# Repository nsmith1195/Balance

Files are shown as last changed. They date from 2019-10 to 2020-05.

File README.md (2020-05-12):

# Balance
<p align="center">
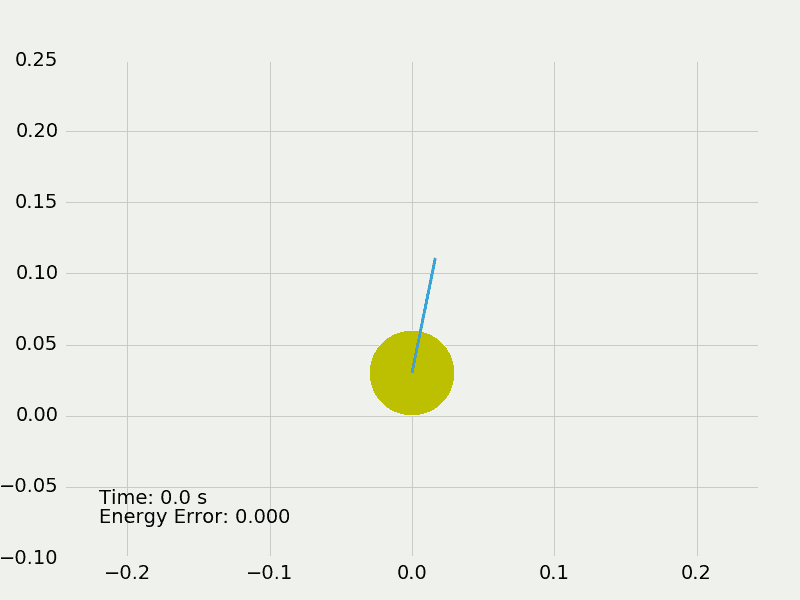
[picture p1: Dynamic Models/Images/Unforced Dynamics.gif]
  
  
</p>

Balancing Robot Repository

Robot acts as an inverted pendulum with the goal of remaining stable while being mobile in at least one direction. Turning may be added as a later feature as wheels are independently actuated. A full report on this project can be found in Final.pdf which includes relevant derivations and explanations for design choices. Below is a short summary of each major section.

## Dynamic Model
The full equations of motion were derived for a Wheeled Inverted Pendulum (WIP) and were used to simulate the system with Scipy. It is assumed that the robot can only move in a straight line which greatly simplifies the calculations. This model was then linearized and used to generate several control laws. 

## Controller Design
To simplify the initial design the linearized model was further reduced to a single input single output transfer function relating the angle of the robot to the torque input. This allows the use of very simple frequency domain design tools such as the root locus, as well as the use of common control architectures like PD and direct feedback.

## Mechanical Design
The body of the robot is mostly composed of secondhand parts from various electronics. Several small parts such as wheel connectors were 3D modeled and printed.

## Electrical Design
The controller for the robot is an Arduino Uno which draws power from the 5 volt regulator on an L298 motor driver. This driver provides power for both motors. To allow for direct control of the torque to each motor, current sensing resistors are placed in series with each motor. To read each voltage a difference amplifier is used to amplify the small voltage drop and allow reading by the Arduinio ADC. Finally, to measure the state of the robot an MPU-6050 inertial measurement unit and quadrature encoders allow direct measurement of the angle and distance travelled. To manage many of these components a breadboard is mounted opposite from the Arduino where each component can easily attach.

## Software Design

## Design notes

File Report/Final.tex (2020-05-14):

\documentclass{article}
\title{Development Of A Wheeled Inverted Pendulum}
\author{Nathan Smith}
\date{April 8th, 2020}

\usepackage{graphicx}
\usepackage{subcaption}
\usepackage{placeins}
\usepackage[margin=1.0in]{geometry}	%Change the page margins to fit long equations
\usepackage{amsmath}

\graphicspath{{"../Report/Images/"}}

%\renewcommand*{\vec}[1]{\mathbf{#1}} %Redefine vector command to make bold instead of overhead arrow

\begin{document}
	\pagenumbering{gobble}
	\maketitle
	
	\newpage
	\tableofcontents

	\newpage
	\pagenumbering{arabic}	
	
	\section{Dynamic Model}
	\subsection{Derivation}
	
	\begin{figure}[h]
		}
		\caption{Overview and Definitions}	
		\label{fig:System Definitions}	
	\end{figure}
	
	As shown in \ref{fig:System Definitions} the configuration of the system is given by x and $\theta$. The variable $\phi$ is the rotation of the wheel relative to the vertical axis and is completely determined by x:
	
	\centerline{$x = r\phi$ and	$\dot{x} = r \dot{\phi}$}
	
	Positive translations are to the right and position rotations are clockwise. Also a positive torque is one which tends to make the WIP accelerate in the positive direction (and cause a negative rotation).

	Since there are two bodies in this system the Euler-Lagrange equation will be used to derive the equations of motion for the WIP:
	\begin{equation}
		\label{eqn:EulerLagrange}	
		\frac{d}{dt}\left(\frac{\partial L}{\partial \dot{q}_i}\right) - \frac{\partial L}{\partial q_i} = F_i
	\end{equation}
	
	where $q = \lbrace x,\theta \rbrace$ are the generalized coordinates defining the configuration of the system and $F = \lbrace \frac{\tau}{r}, -\tau \rbrace$ are the generalized forces acting on each axis. The Lagrangian is also defined as the difference between the kinetic and potential energies of the system: 
	\begin{equation}
		\label{eqn:LagDef}
		L = K - U
	\end{equation}
	
	The Kinetic energy can be expressed as the sum of the translational and rotational kinetic energies of each body:
	$$K = \frac{1}{2} m_1 {\vert \dot{\vec{x}}_1 \vert}^2 + \frac{1}{2}m_2 {\vert \dot{\vec{x}}_2\vert}^2 + \frac{1}{2}J_1 \dot{\phi}^2 + \frac{1}{2}J_2 \dot{\theta}^2$$
	
	\begin{figure}[h]
		\centering
		}
		\caption{Definitions of $\dot{\vec{x}}_1$ and $\dot{\vec{x}}_2$}	
		\label{fig:VectorDefinitions}	
	\end{figure}
	
	To continue ${\vert \dot{\vec{x}}_1 \vert}^2$ and ${\vert \dot{\vec{x}}_2\vert}^2$ must be evaluated. Given the definitions of these vectors in \ref{fig:VectorDefinitions}:
	
	%Define the x1 vector and solve for the square of its magnitude
	$${\vec{x}_1} = x \hat{i}$$
	$$ \dot{\vec{x}}_1 = \dot{x} \hat{i}$$
	$${\vert \dot{\vec{x}}_1 \vert}^2 = \dot{x}^2$$
	
	%Define the x2 vector and solve for square of its magnitude
	$$\vec{x}_2 = (x + Lsin(\theta)\hat{i} + L cos(\theta) \hat{j}$$
	$$\dot{\vec{x}}_2 = (\dot{x} + Lcos(\theta)\dot{\theta})\hat{i} - Lsin(\theta)\dot{\theta}\hat{j}$$
	$$\vert \dot{\vec{x}}_2\vert = \sqrt{(\dot{x} + Lcos(\theta)\dot{\theta})^2 + (-Lsin(\theta) \dot{\theta})^2}$$
	$$\vert \dot{\vec{x}}_2\vert = \sqrt{\dot{x}^2 + 2Lcos(\theta)\dot{x}\dot{\theta} + L^2 cos^2 (\theta)\dot{\theta}^2 + L^2 sin^2(\theta) \dot{\theta}^2}$$
	$${\vert \dot{\vec{x}}_2\vert}^2 = \dot{x}^2 + 2Lcos(\theta)\dot{x}\dot{\theta} + L^2 \dot{\theta}^2$$
	
	Substituting back into the appropriate terms in the Kinetic energy along with the definition of $\phi$:
	$$K = \frac{1}{2}m_1 \dot{x}^2 + \frac{1}{2}m_2 (\dot{x}^2 + 2Lcos(\theta)\dot{x}\dot{\theta} + L^2 \dot{\theta}^2) + \frac{1}{2}J_1 \frac{\dot{x}^2}{r^2} + \frac{1}{2}J_2 \dot{\theta}^2$$
	$$K = \frac{1}{2}(m_1 + m_2 + \frac{J_1}{r^2})\dot{x}^2 + m_2 Lcos(\theta)\dot{x}\dot{\theta} + \frac{1}{2}(m_2 L^2 + J_2)\dot{\theta}^2$$

	This equation is split into three terms, linear acceleration, angular acceleration, and an interaction term between linear and angular velocity. Therefore it seems reasonable to define an effective mass and moment of inertia as $M = m_1 + m_2 + \frac{J_1}{r^2}$ and $I = m_2 L^2 + J_2$.
	
	Substituting these into the Kinetic energy gives:
	\begin{equation}
		\label{eqn:Kinetic}
		K = \frac{1}{2}M\dot{x}^2 + m_2 Lcos(\theta)\dot{x}\dot{\theta} + \frac{1}{2}I\dot{\theta}^2
	\end{equation}
	
	Potential energy can be found as:
	\begin{equation}
		\label{eqn:Potential}
		U = m_2 gLcos(\theta)
	\end{equation}		
	
	Substituting \ref{eqn:Kinetic} and \ref{eqn:Potential} into \ref{eqn:LagDef} gives the full Lagrangian for the system:
	
	\begin{equation}
		\label{eqn:Lagrangian}
		L = \frac{1}{2}M\dot{x}^2 + m_2 Lcos(\theta)\dot{x}\dot{\theta} + \frac{1}{2}I\dot{\theta}^2 - m_2 gLcos(\theta)
	\end{equation}
	
	The Lagrangian must now be substituted into \ref{eqn:EulerLagrange} for each generalized coordinate. Starting with x:
	
	$$\frac{\partial L}{\partial x} = 0$$
	
	$$\frac{\partial L}{\partial \dot{x}} = M\dot{x} + m_2 Lcos(\theta)\dot{\theta}$$
	$$\frac{d}{dt}\left(\frac{\partial L}{\partial \dot{x}}\right) = M\ddot{x} + m_2 Lcos(\theta)\ddot{\theta} - m_2 Lsin(\theta)\dot{\theta}^2$$
	
	\begin{equation}
		\label{eqn:EOM1}
		M\ddot{x} + m_2 Lcos(\theta)\ddot{\theta} - m_2 Lsin(\theta)\dot{\theta}^2 = \frac{\tau}{r}
	\end{equation}		
	
	Equation \ref{eqn:EOM1} is the first equation of motion for the system. Repeating this for $\theta$ will give the second:
	
	$$\frac{\partial L}{\partial \theta} = -m_2 Lsin(\theta) \dot{x}\dot{\theta} + m_2 gLsin(\theta)$$
	
	$$\frac{\partial L}{\partial \dot{\theta}} = m_2 Lcos(\theta)\dot{x} + I\dot{\theta}$$
	$$\frac{d}{dt} \left( \frac{\partial L}{\partial \dot{\theta}} \right) = m_2 Lcos(\theta)\ddot{x} - m_2 Lsin(\theta)\dot{x}\dot{\theta} + I\ddot{\theta}$$
	
	\begin{equation}
		\label{eqn:EOM2}
		m_2 Lcos(\theta)\ddot{x} - m_2 Lsin(\theta)\dot{x}\dot{\theta} + I\ddot{\theta} + m_2 Lsin(\theta) \dot{x}\dot{\theta} - m_2 gLsin(\theta) = -\tau
	\end{equation}
	
	Equations \ref{eqn:EOM1} and \ref{eqn:EOM2} both depend on $\ddot{x}$ and $\ddot{\theta}$ and must be solved in terms of these simultaneously. Doing this yields:
	
	\begin{equation}
		\label{eqn:linAcc}
		\ddot{x} = - \frac{m_2 LIsin(\theta)}{m_2^2 L^2 cos(\theta) - MI}\dot{\theta}^2 + \frac{m_2^2 L^2 g}{m_2^2 L^2 cos(\theta) - MI}cos(\theta)sin(\theta) - \left[ \frac{I + rm_2 Lcos(\theta)}{r(m_2^2 L^2 cos(\theta) - MI)} \right] \tau
	\end{equation}
	
	\begin{equation}
		\label{eqn:angAcc}
		\ddot{\theta} = \frac{m_2^2 L^2 sin(\theta)}{m_2^2 L^2 cos(\theta) - MI}\dot{\theta}^2 - \frac{Mm_2 gLsin(\theta)}{m_2^2 L^2 cos(\theta) - MI} + \left[ \frac{rM + m_2 L}{r(m_2^2 L^2 cos(\theta) - MI)} \right] \tau
	\end{equation}
	
	These two non-linear equations describe the motion of the system in the configuration space. To make simulation easier these are converted into the state space by adding the velocities associated with each coordinate:
	
	\begin{equation}
		\label{eqn:nonLinSS}
		\begin{bmatrix}
			\dot{x} 		\\
			\ddot{x}		\\
			\dot{\theta}	\\
			\ddot{\theta}
		\end{bmatrix}
		=		
		\begin{bmatrix}
			\dot{x}			\\
			-\frac{m_2 LIsin(\theta)}{m_2^2 L^2 cos(\theta) - MI}\dot{\theta}^2 + \frac{m_2^2 L^2 g}{m_2^2 L^2 cos(\theta) - MI}cos(\theta)sin(\theta)			\\
			\dot{\theta}	\\
			\frac{m_2^2 L^2 sin(\theta)}{m_2^2 L^2 cos(\theta) - MI}\dot{\theta}^2 - \frac{Mm_2 gLsin(\theta)}{m_2^2 L^2 cos(\theta) - MI}
		\end{bmatrix}
		+
		\begin{bmatrix}
			0																	\\
			-\frac{I + rm_2 Lcos(\theta)}{r(m_2^2 L^2 cos(\theta) - MI)}		\\
			0																	\\
			\frac{rM + m_2 L}{r(m_2^2 L^2 cos(\theta) - MI)}
		\end{bmatrix}
		\tau
	\end{equation}
	
	\subsection{Linearization}
	Equation \ref{eqn:nonLinSS} can be easily simulated with tools such as Scipy's ODEint function to create a reasonable representation of the system. It is not, however, easy to develop control laws for a non-linear system and so it is necessary to linearize it. This will be done about the upwards stationary point $\vec{x}^* = [x, 0, 0, 0]^T$. There is an x in this state since there is a symmetry in x. Currently the system is of the form:
	
	\centerline{$\dot{\vec{x}} = \vec{f}(\vec{x},u)$, where in this case $u = \tau$}
	Linearizing would put the system into the form:
	$$\dot{\vec{x}} = A\vec{x} + Bu$$
	
	To generate A and B the following formula must be applied:
	$A = \left[ \frac{\partial \vec{f}(\vec{x},u)}{\partial \vec{x}} \right]_{x^*,u^*}$ and $B = \left[ \frac{\partial \vec{f}(\vec{x},u)}{\partial u} \right]_{x^*,u^*}$
	
	Doing so yields:
	
	\begin{equation}
		\label{eqn:linSS}
		A = \begin{bmatrix}
			0 & 1 & 0 & 0	\\
			0 & 0 & \frac{m_2^2 L^2 g}{m_2^2 L^2 - MI} & 0 \\
			0 & 0 & 0 & 1	\\
			0 & 0 & -\frac{Mm_2 gL}{m_2^2 L^2 - MI} & 0
		\end{bmatrix}
		\quad and	\quad B = \begin{bmatrix}
			0	\\
			-\frac{I + rm_2 L}{r(m_2^2 L^2 - MI)}	\\
			0	\\
			\frac{rM + m_2 L}{r(m_2^2 L^2 - MI)}
		\end{bmatrix}
	\end{equation}
	
	The output equation will initially return only $\theta$ and so will be:
	
	$y = \vec{C} \vec{x} + Du$, where $\vec{C} = [0, 0, 1, 0] and D = 0$ 
	
	\subsection{Transfer Function}
	Due to some quirks in the Python-Controls library with regards to analyzing state space models, the state space representation derived will be converted into a transfer function to make analysis easier to interpret. Doing so uses:
	
	\begin{equation}
		\label{eqn:SS2TF}
		\frac{\theta (s)}{\tau (s)} = \vec{C}(sI - A)^{-1}\vec{B} + D
	\end{equation}
	
	Applying this to the current system gives:
	
	\begin{equation}
		\label{eqn:SISOTF}
		\frac{\theta (s)}{\tau (s)} = \frac{a}{s^2 - b}
	\end{equation}
	
	\centerline{where $a = \frac{rM + m_2 L}{r(m_2^2 L^2 - MI)}$ and $b = -\frac{Mm_2 gL}{m_2^2 L^2 - MI}$}

	\section{Controller Design}
	\subsection{Plant analysis}
	
	\begin{figure}[h]
		\centerline{}}
		\caption{Pole Zero map of the transfer function. The two poles are real and symmetric, one always in the right half plane.}
		\label{fig:PlantPZMap}	
	\end{figure}	
	
	Figure \ref{fig:PlantPZMap} shows the pole zero map of equation \ref{eqn:SISOTF}, it can be seen that one of the poles is in the right half plane and so the system is unstable. 
	
	\subsection{Direct Feedback Design with Root Locus}
	
	\begin{figure}[h]
		\centerline{}
		\caption{Root locus plot of the plant. Larger gains only yield marginal stability.}
		\label{fig:DirectFeedRL}
	\end{figure}
	
	As a first attempt to stabilize the WIP a simple gain controller was implemented in the simulation. As shown in figure \ref{fig:DirectFeedRL} the system is unstable for low gains and only achieves marginal stability with larger gains. This is not acceptable as a solution but does make for an interesting animation which can be seen in the readme for this project.
		
	\subsection{PD Design}
	While continuous time PD controllers are not realizeable, the fact that my simulation provides access to the entire state of the system I am able to sidestep this limitation though when it is implemented on hardware the controller will need to be discretized. The usual form of a PD controller is:
	
	\begin{equation}
		\label{eqn:PDController}
		C(s) = k_d s + k_p
	\end{equation}
	
	This equation has two parameters to vary and so makes traditional design techniques such as root locus design difficult. By factoring out $k_d$ this becomes slightly easier since the pole can be placed by hand at the point $-\frac{k_p}{k_d}$ and $k_d$ can be used as the root locus gain. Doing this gives the modified PD transfer function:
	
	\begin{equation}
		\label{eqn:PDModified}
		C(s) = k_d (s + \frac{k_p}{k_d})
	\end{equation}
	
	The PD controller effectively adds a zero to the function and in this form the ratio $\frac{k_p}{k_d}$ decides that zero's location. Since both system poles and the zero are on the real axis, the zero can either be between the open loop poles $\frac{k_p}{k_d} < b$ or to the left of them $\frac{k_p}{k_d} > b$. To get reasonably quick dynamics the latter case should be selected. 
	
	\begin{figure}[h]
		\centerline{}
		\caption{Root Locus plot of the plant with a PD controller. K value in image is $k_d$ and the location of the zero is $-\frac{k_p}{k_d}$}
		\label{fig:PDRootLocus}
	\end{figure}
	
	The right plot of figure \ref{fig:PDRootLocus} shows the more desirable case. As can be seen in that plot from the annotated gains, even a gain as small as 0.12 will move the dominant pole very close to the zero. The non-dominant pole is far in the negative direction and was excluded from the figure in the interest of maintaining a reasonable scale and readability.

\section{Mechanical Design}

	\begin{figure}[h]
		\centerline{}
		\caption{Expected setup of robot body. Some areas such as the method of attaching the wheels are still undetermined.}		
		\label{fig:RobotBodyGraphic}
	\end{figure}

	\subsection{Part Sourcing}
	Due to the very limited budget for this project most parts were scavenged from old printers and toys. Most structural parts came from a toy erectors set which allowed for some degree of uniformity in the design due to those components having regularly spaced holes. The motor mounts were made by cutting the entire motor assembly along with the encoders out of an old printer and mounting them in the best possible way to the sides of the body. This approach led to many issues of alignment with regards to the Inertial Measurement Unit (IMU) which required extra effort to calibrate. 	

	\subsection{Custom Parts}
	Since the gears attached to the wheels were not designed to mount the wheels I had on hand, I had to design a custom adaptor to allow the wheels to mount. 
	
	\subsection{Mass Properties}
	Due to the largely unplanned nature of the mechanical design the mass properties of the robot must be measured after each section is assembled. The names for each section of the robot will follow the same convention as the derivation of the equations of motion, namely body 1 references the wheels and body 2 references the main body of the robot. The masses of each are easy to obtain using a standard scale, however the moments of inertia of each are more difficult to establish.

	\begin{figure}[h]
		\centerline{}
		\caption{Experimental setup and diagram of forces acting on body 1. Polar coordinates are initially used to define the location of the body where $\theta$ is the angle of the ramp and x is the distance of the body from the bottom.}
		\label{fig:Body1MassProps}
	\end{figure}		
	
	The moment of inertia of body 1 will be found by rolling it down a long inclined plane and timing it.	 A description of this setup is shown in figure \ref{fig:Body1MassProps}. Polar coordinates were used to define the location of the body with x being the radial distance from the origin. Due to this the velocity found is negative but this decision doesn't change the results. The variable $\phi$ defines the angular position of the body and is related to x through the equation: 
	
											%Definition of phi
	\begin{equation}
		\label{eqn:Body1PropsPhiDefinition}
		L - x = r\phi
	\end{equation}
	
	$$-\dot{x} = r \dot{\phi}$$
	
	\begin{equation}
		-\ddot{x} = r \ddot{\phi}
		\label{eqn:Body1PropsPhiddot}
	\end{equation}
	
	Using the coordinate system in figure \ref{fig:Body1MassProps} force and torque balances can be calculated:
	
	%Force balance in x
	$$\Sigma F_x = ma_x = \mu N - mgsin(\theta)$$
	
	Solving for the coefficient of static friction $\mu$:	
	\begin{equation}
		\mu = \frac{a_x + gsin(\theta)}{gcos(\theta)}
		\label{eqn:Body1PropsMu1}
	\end{equation}
	
	%Torque balance about CG
	The torque balance is done about the body's center of mass:
	$$\Sigma M_{CG} = J\ddot{\phi} = r \mu mgcos(\theta)$$
	
	Again solving for $\mu$:
	\begin{equation}
		\mu = \frac{J\ddot{\phi}}{rmgcos(\theta)}
		\label{eqn:Body1PropsMu2}
	\end{equation}
	
	Equating \ref{eqn:Body1PropsMu1} and \ref{eqn:Body1PropsMu2}:
	$$\frac{a_x + gsin(\theta)}{gcos(\theta)} = \frac{J\ddot{\phi}}{rmgcos(\theta)}$$
	
	Simplifying:
	$$a_x + gsin(\theta) = \frac{J\ddot{\phi}}{mr}$$
	
	Substituting equation \ref{eqn:Body1PropsPhiddot} for $\ddot{\phi}$:
	$$a_x + gsin(\theta) = -\frac{Ja_x}{mr^2}$$
	
	$$\left[ 1 + \frac{J}{mr^2} \right] a_x = -gsin(\theta)$$
	$$a_x = -gsin(\theta)\frac{mr^2}{J + mr^2}$$
	
	Integrating both sides with respect to time:
	$$\int_{v_0}^{v} dv = -gsin(\theta)\frac{mr^2}{J + mr^2} \int_{0}^{t} dt$$
	
	The initial velocity is assumed to be zero:
	$$v = -gsin(\theta)\frac{mr^2}{J + mr^2}t$$
	
	Integrating again:
	$$\int_{L}^{0} dx = -gsin(\theta)\frac{mr^2}{J + mr^2} \int_{0}^{T_f} t dt$$
	
	$$-L = -gsin(\theta)\frac{mr^2}{J + mr^2}\frac{T_f^2}{2}$$
	
	Finally rearranging:
	$$J_{eff} = J + mr^2 = \frac{gmr^2sin(\theta)}{L} \frac{T_f^2}{2}$$
	
	This is the moment of inertia about the contact point with the ground and is the effective moment of inertia of the rolling body.
	
	\begin{figure}[h]
		\centerline{}
		\caption{Comparison between the actual geometry of body 2 and the idealized physical pendulum.}
		\label{fig:Body2MassProps}
	\end{figure}
	The moment of inertia of body 2 can be found relatively simply by noting that it effectively is a physical pendulum. By allowing body 2 to hang by its pivot point with the wheels removed and allowing it to swing freely the natural frequency of oscillation can be measured. This quantity can be used to calculate the moment of inertia for the body about the pivot point. This measured value is about the pivot point of the wheels and can also be expressed about the center of mass of the body. Starting with a torque balance of the pendulum:
	\begin{equation}
		\label{eqn:PhysicalPendTorqueBalance}
		\Sigma M_0 = J_{eff} \alpha = -mgLsin(\theta)
	\end{equation}
	
	To eliminate the non-linearity in $\theta$ only small angles are permitted. This allows the approximation $\theta \approx sin(\theta)$ to be used:
	
	$$\alpha = \frac{d^2 \theta}{dt^2} = -\frac{mgL}{J_{eff}}\theta$$
	
	\begin{equation}
		\label{eqn:PhysicalPendLinearODE}
		\frac{d^2 \theta}{dt^2} + \frac{mgL}{J_{eff}} = 0
	\end{equation}
	
	Using standard methods for solving ODE's, if the solution is assumed to be of the form $\theta = e^{rt}$ then the characteristic equation for this system is:
	$$r^2 + \frac{mgL}{J_{eff}} = 0$$
	$$r^2 = -\frac{mgL}{J_{eff}}$$
	$$r = \pm \sqrt[•]{-\frac{mgL}{J_{eff}}}$$
	$$r = \pm i \; \sqrt[•]{\frac{mgL}{J_{eff}}}$$  % \; is a small space to keep sqrt from overlapping i
	
	Plugging these roots into the assumed solution yields:
	$$\theta = c_1 e^{i \; \sqrt[•]{\frac{mgL}{J_{eff}}}t} + c_2 e^{-i \; \sqrt[•]{\frac{mgL}{J_{eff}}}t}$$
	
	Applying Euler's formula:
	$$\theta = c_1 cos(\; \sqrt[•]{\frac{mgL}{J_{eff}}}t) + i c_2 sin(\; \sqrt[•]{\frac{mgL}{J_{eff}}}t)$$
	
	Taking the real part and applying initial conditions:
	\begin{equation}
		\label{fig:PhysicalPendRealSolution}
		\theta = \theta_0 cos(\; \sqrt[•]{\frac{mgL}{J_{eff}}}t)
	\end{equation}

	%equate to w0 and solve for J_eff
	
	Noting that the argument $\sqrt[•]{\frac{mgL}{J_{eff}}}$ is the natural frequency, $\omega_0$, in terms of angular frequency. This can be expressed in terms of frequency:
	$$\omega_0 = 2\pi f_0$$
	
	$$f_0 = \frac{1}{2\pi} \; \sqrt[•]{\frac{mgL}{J_{eff}}}$$
	
	The frequency can be measured by allowing the body to swing and counting the number of cycles which occur over a set time period. This can now be solved for the effective moment of inertia:
	
	$$2\pi f_0 = \sqrt[•]{\frac{mgL}{J_{eff}}}$$
	
	$$4\pi^2 f_0^2 = \frac{mgL}{J_{eff}}$$
	
	\begin{equation}
		\label{eqn:Body2EffectiveMomentOfInertia}
		J_{eff} = \frac{mgL}{4\pi^2 f_0^2}
	\end{equation}
	
	This effective moment of inertia can be used directly in the dynamic model of the system as it is about the axis of rotation. If the moment of inertia about the center of mass is necessary the parallel axis theorem could be applied to yield:
	$$J_{CG} = \frac{mgL}{4\pi^2 f_0^2} - mL^2$$ 

\section{Electrical Design}
	\subsection{Component Selection}
	To control the robot an Arduino microcontroller was used as it was available at the start of the project. While the Arduino isn't the fastest controller available it should be more than fast enough for this project.
	Both motors will be driven by a single L298-n motor driver circuit. This chip also has a 5 volt regulated output and will be used to provide power to the Arduino and IMU. 
	In order to measure the orientation of the robot an MPU-6050 Inertial Measurement Unit was used.

	\subsection{Motor Parameter Evaluation}
	\begin{figure}[h]
		\centerline{}
		\caption{Overview of setup. $\omega_s$ can be measured directly and related to $\omega_m$ through geometry. The back emf, $e_a$, can be measured directly as well.}
		\label{fig:DirectFeedRL}
	\end{figure}
	
	For a permanent magnet DC motor the following relationships hold\cite{Ogata}:
	$$\tau = KI$$
	$$$$

\section{Software Design}
	\subsection{Component Testing Software}
	
	\subsection{Controller Software}
	
\begin{thebibliography}{9}	%Number 9 doesn't mean anything. The number of digits determines how many refs can be made in bibliography. i.e. 1,6, or 8 would allow up to 9 refs while 13 would allow 99, etc.

	\bibitem{Ogata}
		Katsuhiko Ogata,
		\textit{System Dynamics},
		4th edition,
		2004.

\end{thebibliography}

\end{document}

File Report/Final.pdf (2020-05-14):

# Development Of A Wheeled Inverted Pendulum

Nathan Smith

April 8th, 2020

## Contents

1 Dynamic Model | 1
2 Controller Design | 4
3 Mechanical Design | 5
4 Electrical Design | 9
5 Software Design | 10

## 1 Dynamic Model

### 1.1 Derivation

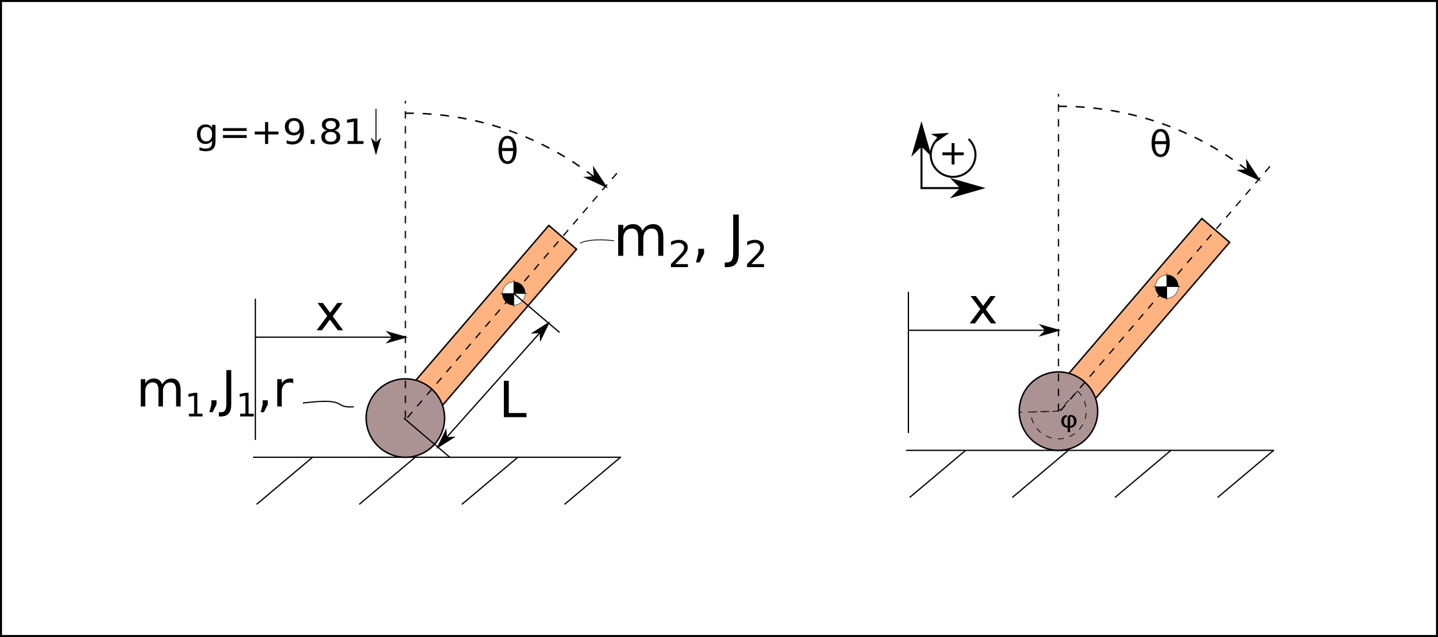
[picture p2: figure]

Figure 1: Overview and Definitions

As shown in 1 the configuration of the system is given by x and θ. The variable φ is the rotation of the wheel relative to the vertical axis and is completely determined by x:
x = rφ and ẋ = rφ˙
Positive translations are to the right and position rotations are clockwise. Also a positive torque is one which tends to make the WIP accelerate in the positive direction (and cause a negative rotation).
Since there are two bodies in this system the Euler-Lagrange equation will be used to derive the equations of motion for the WIP:
d

dt
∂L
∂q˙i
−

∂L
∂qi
= Fi | (1)

where q = {x, θ} are the generalized coordinates defining the configuration of the system and F = {

τ
r
| , −τ}
are the generalized forces acting on each axis. The Lagrangian is also defined as the difference between the kinetic and potential energies of the system:
L = K − U | (2)

The Kinetic energy can be expressed as the sum of the translational and rotational kinetic energies of each body:

K =

1
2

m1|

˙~x1|

2
+

1
2

m2|

˙~x2|

2
+

1
2

J1φ˙² +

1
2

J2

˙θ
2

To continue |

˙~x1|

2
and |

˙~x2|

2
must be evaluated. Given the definitions of these vectors in 2:

~x1 = xî

˙~x1 = ẋî

˙~x1|

2
= ẋ

2

~x2 = (x + Lsin(θ)î + Lcos(θ)ĵ

˙~x2 = ( ẋ + Lcos(θ)
˙θ)î − Lsin(θ)

˙θĵ

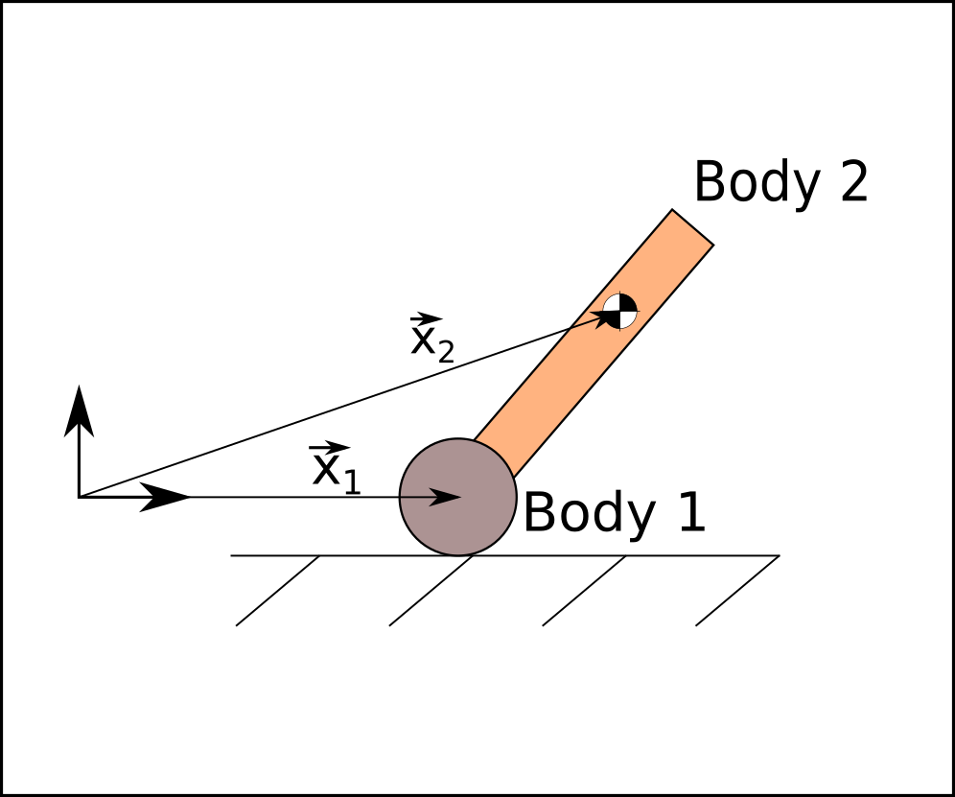
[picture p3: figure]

Figure 2: Definitions of ˙~x1 and ˙~x2

˙~x2| =

q
( ẋ + Lcos(θ)

˙θ)
2 + (−Lsin(θ)

˙θ)
2

˙~x2| =

q
x˙

2 + 2Lcos(θ) ẋ ˙θ + L²cos²(θ)

˙θ
2 + L²sin²(θ)

˙θ
2

˙~x2|

2
= ẋ

2 + 2Lcos(θ) ẋ ˙θ + L

2 ˙θ
2

Substituting back into the appropriate terms in the Kinetic energy along with the definition of φ:

K =

1
2

m1x˙

2 +

1
2

m2( ẋ

2 + 2Lcos(θ) ẋ ˙θ + L

2 ˙θ
2

) + 1
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
(m1 + m2 +

J1
r

2

) ẋ

2 + m2Lcos(θ) ẋ ˙θ +

1
2

(m2L

2 + J2)

˙θ
2

This equation is split into three terms, linear acceleration, angular acceleration, and an interaction term between linear and angular velocity. Therefore it seems reasonable to define an effective mass and moment of inertia as M = m1 + m2 +

J1
r

2 and I = m2L

2 + J2.
Substituting these into the Kinetic energy gives:

K =

1
2

Mx˙

2 + m2Lcos(θ) ẋ ˙θ +

1
2

I

˙θ
2
(3)

Potential energy can be found as:
U = m2gLcos(θ) | (4)

Substituting 3 and 4 into 2 gives the full Lagrangian for the system:

L =

1
2

Mx˙

2 + m2Lcos(θ) ẋ ˙θ +

1
2

I

˙θ
2 − m2gLcos(θ) | (5)

The Lagrangian must now be substituted into 1 for each generalized coordinate. Starting with x:

∂L
∂x = 0

∂L
∂x˙

= Mx˙ + m2Lcos(θ)

˙θ

d

dt
∂L
∂x˙
= Mx¨ + m2Lcos(θ)

¨θ − m2Lsin(θ)
˙θ
2

Mx¨ + m2Lcos(θ)

¨θ − m2Lsin(θ)

˙θ
2 =

τ
r

(6)

Equation 6 is the first equation of motion for the system. Repeating this for θ will give the second:

∂L
∂θ = −m2Lsin(θ) ẋ ˙θ + m2gLsin(θ)

∂L
∂ ˙θ

= m2Lcos(θ) ẋ + I

˙θ

d

dt
∂L
∂ ˙θ
= m2Lcos(θ)ẍ − m2Lsin(θ) ẋ ˙θ + I

¨θ

m2Lcos(θ)ẍ − m2Lsin(θ) ẋ ˙θ + I

¨θ + m2Lsin(θ) ẋ ˙θ − m2gLsin(θ) = −τ | (7)

Equations 6 and 7 both depend on ẍ and ¨θ and must be solved in terms of these simultaneously. Doing this yields:

x¨ = −

m2LIsin(θ)
m²
2L²cos(θ) − MI

˙θ
2 +

m²
2L

2
g
m²
2L²cos(θ) − MI

cos(θ)sin(θ) −

I + rm2Lcos(θ)
r(m²
2L²cos(θ) − MI)
τ | (8)

¨θ =

m²
2L

2
sin(θ)
m²
2L²cos(θ) − MI

˙θ
2 −

Mm2gLsin(θ)
m²
2L²cos(θ) − MI

+

rM + m2L
r(m²
2L²cos(θ) − MI)
τ | (9)

These two non-linear equations describe the motion of the system in the configuration space. To make simulation easier these are converted into the state space by adding the velocities associated with each coordinate:

x˙
x¨
˙θ
¨θ

=

x˙
−

m2LIsin(θ)
m²
2L²cos(θ)−M I

˙θ
2 +

m²
2L

2
g
m²

2L²cos(θ)−M I cos(θ)sin(θ) ˙θ

m²
2L

2
sin(θ)
m²
2L²cos(θ)−M I

˙θ
2 −

Mm2gLsin(θ)
m²
2L²cos(θ)−M I

+

0
−

I+rm2Lcos(θ)
r(m²
2L²cos(θ)−M I)
0
rM+m2L
r(m²
2L²cos(θ)−M I)

τ | (10)

### 1.2 Linearization

Equation 10 can be easily simulated with tools such as Scipy’s ODEint function to create a reasonable representation of the system. It is not, however, easy to develop control laws for a non-linear system and so it is necessary to linearize it. This will be done about the upwards stationary point ~x∗ = [x, 0, 0, 0]T
. There
is an x in this state since there is a symmetry in x. Currently the system is of the form:
˙~x = ~f(~x, u), where in this case u = τ Linearizing would put the system into the form:

˙~x = A~x + Bu

To generate A and B the following formula must be applied: A =

h

∂f~(~x,u)
∂~x i

x∗,u∗

and B =

h

∂f~(~x,u)
∂u i

x∗,u∗
Doing so yields:

A =

0 1 | 0 | 0
0 0 | m² 2L

2
g
m²
| 2L²−M I | 0
0 0 | 0 | 1
0 0 − | Mm2gL
m²
| 2L²−M I | 0

and B =

0
−

I+rm2L
r(m²
2L²−M I)
0
rM+m2L
r(m²
2L²−M I)

(11)

The output equation will initially return only θ and so will be: y = C~x~ + Du, where C~ = [0, 0, 1, 0]andD = 0

### 1.3 Transfer Function

Due to some quirks in the Python-Controls library with regards to analyzing state space models, the state space representation derived will be converted into a transfer function to make analysis easier to interpret. Doing so uses:

θ(s)
τ (s)

= C~ (sI − A)

−1B~ + D | (12)

Applying this to the current system gives:

θ(s)
τ (s)

=

a
s

2 − b

(13)

where a =

rM+m2L
r(m²
2L²−M I)

and b = −

Mm2gL
m²
2L²−M I

## 2 Controller Design

### 2.1 Plant analysis

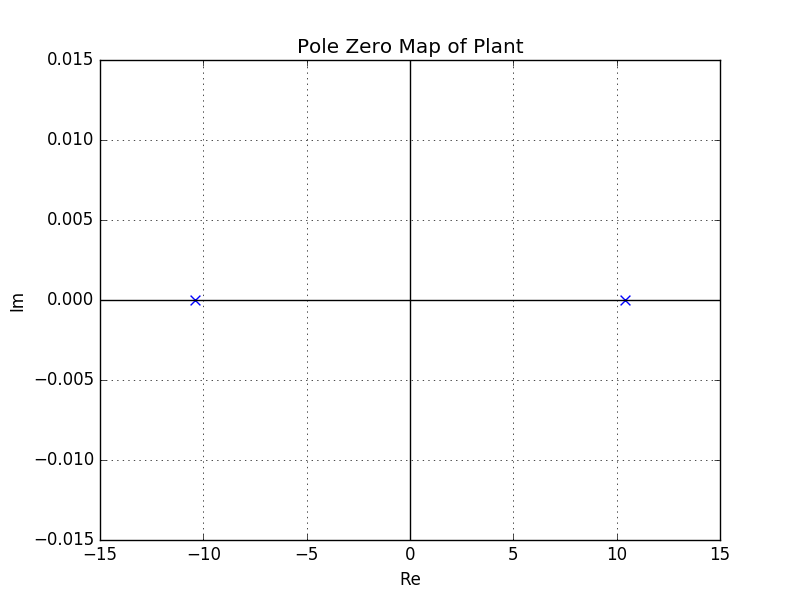
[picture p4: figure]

Figure 3: Pole Zero map of the transfer function. The two poles are real and symmetric, one always in the right half plane.

Figure 3 shows the pole zero map of equation 13, it can be seen that one of the poles is in the right half plane and so the system is unstable.

### 2.2 Direct Feedback Design with Root Locus

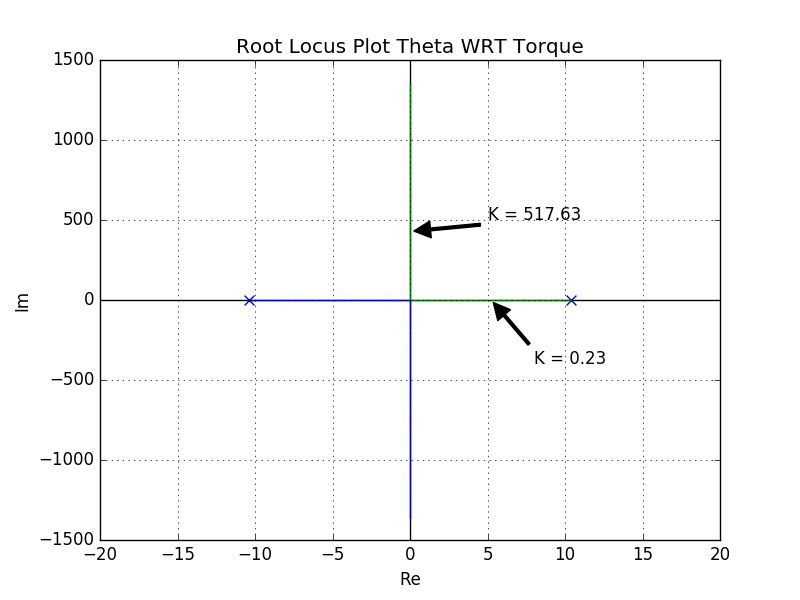
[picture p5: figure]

Figure 4: Root locus plot of the plant. Larger gains only yield marginal stability.

As a first attempt to stabilize the WIP a simple gain controller was implemented in the simulation. As shown in figure 9 the system is unstable for low gains and only achieves marginal stability with larger gains. This is not acceptable as a solution but does make for an interesting animation which can be seen in the readme for this project.

### 2.3 PD Design

While continuous time PD controllers are not realizeable, the fact that my simulation provides access to the entire state of the system I am able to sidestep this limitation though when it is implemented on hardware the controller will need to be discretized. The usual form of a PD controller is:

C(s) = kds + kp | (14)

This equation has two parameters to vary and so makes traditional design techniques such as root locus design difficult. By factoring out kd this becomes slightly easier since the pole can be placed by hand at the point −

kp
kd

and kd can be used as the root locus gain. Doing this gives the modified PD transfer function:

C(s) = kd(s +

kp
kd
) | (15)

The PD controller effectively adds a zero to the function and in this form the ratio kp
kd
| decides that zero’s
location. Since both system poles and the zero are on the real axis, the zero can either be between the open loop poles kp
kd

< b or to the left of them kp
kd

> b. To get reasonably quick dynamics the latter case should be selected.

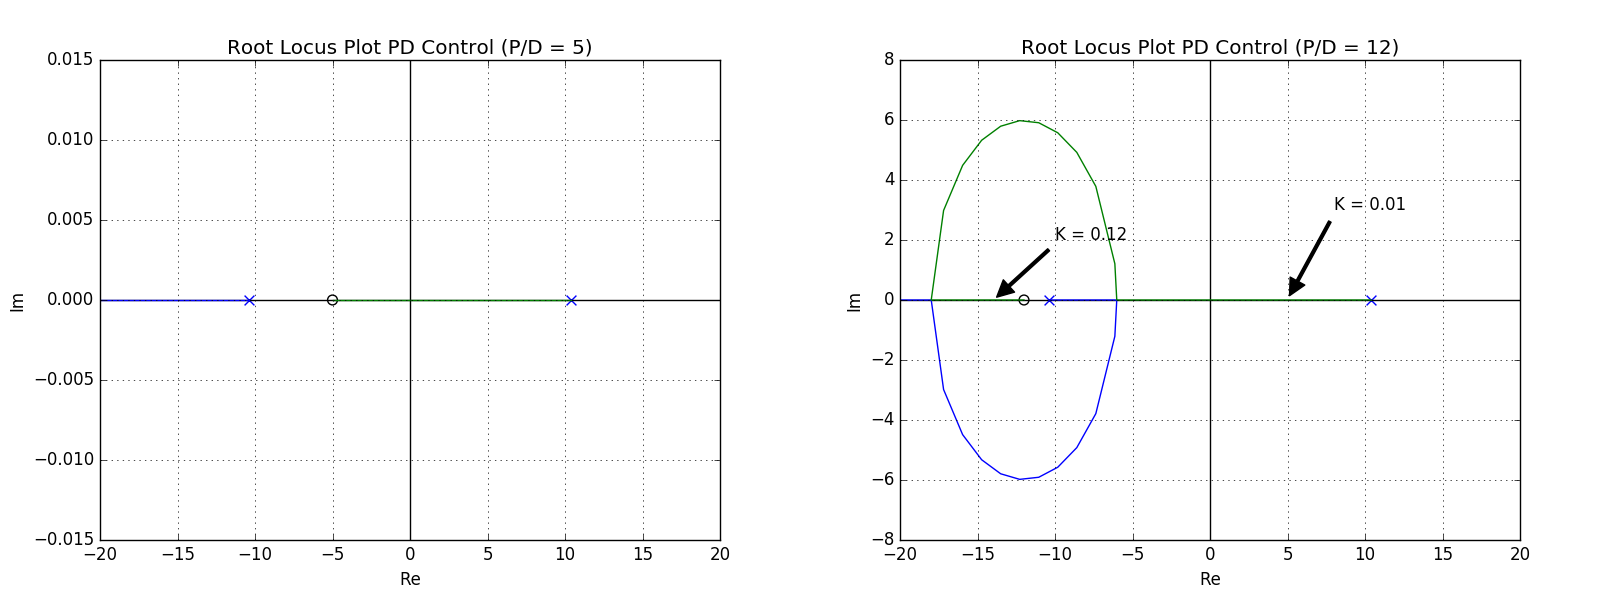
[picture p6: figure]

Figure 5: Root Locus plot of the plant with a PD controller. K value in image is kd and the location of the zero is −

kp
kd

The right plot of figure 5 shows the more desirable case. As can be seen in that plot from the annotated gains, even a gain as small as 0.12 will move the dominant pole very close to the zero. The non-dominant pole is far in the negative direction and was excluded from the figure in the interest of maintaining a reasonable scale and readability.

## 3 Mechanical Design

### 3.1 Part Sourcing

Due to the very limited budget for this project most parts were scavenged from old printers and toys. Most structural parts came from a toy erectors set which allowed for some degree of uniformity in the design due to those components having regularly spaced holes. The motor mounts were made by cutting the entire motor assembly along with the encoders out of an old printer and mounting them in the best possible way to the sides of the body. This approach led to many issues of alignment with regards to the Inertial Measurement Unit (IMU) which required extra effort to calibrate.

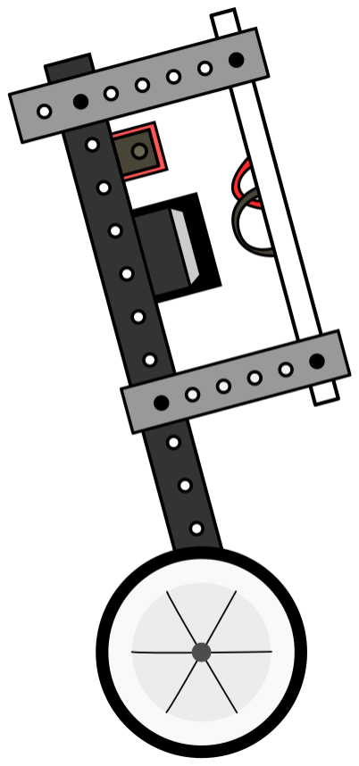
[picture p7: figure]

Figure 6: Expected setup of robot body. Some areas such as the method of attaching the wheels are still undetermined.

### 3.2 Custom Parts

Since the gears attached to the wheels were not designed to mount the wheels I had on hand, I had to design a custom adaptor to allow the wheels to mount.

### 3.3 Mass Properties

Due to the largely unplanned nature of the mechanical design the mass properties of the robot must be measured after each section is assembled. The names for each section of the robot will follow the same convention as the derivation of the equations of motion, namely body 1 references the wheels and body 2 references the main body of the robot. The masses of each are easy to obtain using a standard scale, however the moments of inertia of each are more difficult to establish.

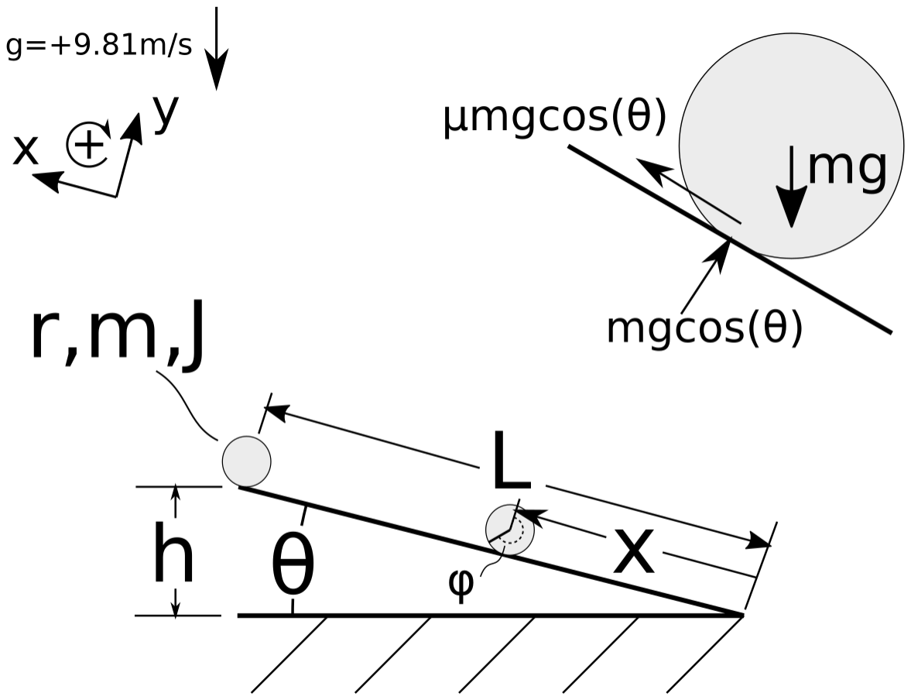
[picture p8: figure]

Figure 7: Experimental setup and diagram of forces acting on body 1. Polar coordinates are initially used to define the location of the body where θ is the angle of the ramp and x is the distance of the body from the bottom.

The moment of inertia of body 1 will be found by rolling it down a long inclined plane and timing it. A description of this setup is shown in figure 7. Polar coordinates were used to define the location of the body with x being the radial distance from the origin. Due to this the velocity found is negative but this decision doesn’t change the results. The variable φ defines the angular position of the body and is related to x through the equation:

L − x = rφ | (16)

−x˙ = rφ˙

−x¨ = rφ¨ | (17)

Using the coordinate system in figure 7 force and torque balances can be calculated:

ΣFx = max = µN − mgsin(θ)

Solving for the coefficient of static friction µ:

µ =

ax + gsin(θ)
gcos(θ)

(18)

The torque balance is done about the body’s center of mass:

ΣMCG = Jφ¨ = rµmgcos(θ)

Again solving for µ:

µ =

Jφ¨
rmgcos(θ)

(19)

Equating 18 and 19:
ax + gsin(θ)
gcos(θ)

=

Jφ¨
rmgcos(θ)

Simplifying:
ax + gsin(θ) = Jφ¨

mr
Substituting equation 17 for φ¨:

ax + gsin(θ) = −

Jax
mr²
1 +

J
mr²
ax = −gsin(θ)

ax = −gsin(θ)

mr²
J + mr²
Integrating both sides with respect to time:
Z v

v0

dv = −gsin(θ)

mr²
J + mr²

Z t

0

dt

The initial velocity is assumed to be zero:

v = −gsin(θ)

mr²
J + mr²

t

Integrating again:
Z 0

L

dx = −gsin(θ)

mr²
J + mr²

# Z Tf

0

tdt

−L = −gsin(θ)

mr²
J + mr²

T

2
f
2
Finally rearranging:

Jef f = J + mr² =

gmr²
sin(θ)
L

T

2
f
2
This is the moment of inertia about the contact point with the ground and is the effective moment of inertia of the rolling body.

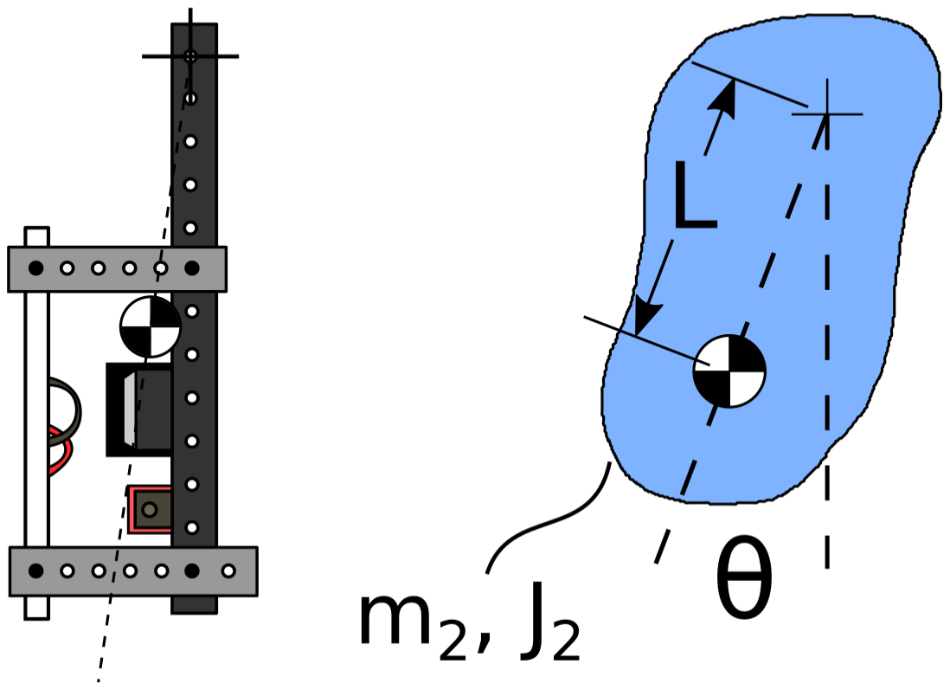
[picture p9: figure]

Figure 8: Comparison between the actual geometry of body 2 and the idealized physical pendulum.

The moment of inertia of body 2 can be found relatively simply by noting that it effectively is a physical pendulum. By allowing body 2 to hang by its pivot point with the wheels removed and allowing it to swing freely the natural frequency of oscillation can be measured. This quantity can be used to calculate the moment of inertia for the body about the pivot point. This measured value is about the pivot point of the wheels and can also be expressed about the center of mass of the body. Starting with a torque balance of the pendulum:
ΣM0 = Jef fα = −mgLsin(θ) | (20)

To eliminate the non-linearity in θ only small angles are permitted. This allows the approximation θ ≈ sin(θ) to be used:

α =

d

2
θ
dt²

= −

mgL

Jef f

θ

d

2
θ
dt²

+

mgL

Jef f

= 0 | (21)
Using standard methods for solving ODE’s, if the solution is assumed to be of the form θ = e | rt then the
characteristic equation for this system is:

r

2 +

mgL

Jef f

= 0

r

2 = −

mgL

Jef f

r = ±

s
−

mgL

Jef f

r = ±i

s
mgL

Jef f

Plugging these roots into the assumed solution yields:

θ = c1e

i

q mgL
Jeff

t
+ c2e

−i

q mgL
Jeff

t

Applying Euler’s formula:

θ = c1cos(

s
mgL

Jef f

t) + ic2sin(

s
mgL

Jef f

t)

Taking the real part and applying initial conditions:

θ = θ0cos(

s
mgL

Jef f

t) (22)

Noting that the argumentq mgL

Jeff

is the natural frequency, ω0, in terms of angular frequency. This can be expressed in terms of frequency: ω0 = 2πf0

f0 =

1
2π

s
mgL

Jef f

The frequency can be measured by allowing the body to swing and counting the number of cycles which occur over a set time period. This can now be solved for the effective moment of inertia:

2πf0 =

s
mgL

Jef f

4π

2
f

2
0 =

mgL

Jef f

Jef f =

mgL
4π

2f

2
0

(23)

This effective moment of inertia can be used directly in the dynamic model of the system as it is about the axis of rotation. If the moment of inertia about the center of mass is necessary the parallel axis theorem could be applied to yield:

JCG =

mgL
4π

2f

2
0

− mL²

## 4 Electrical Design

### 4.1 Component Selection

To control the robot an Arduino microcontroller was used as it was available at the start of the project. While the Arduino isn’t the fastest controller available it should be more than fast enough for this project. Both motors will be driven by a single L298-n motor driver circuit. This chip also has a 5 volt regulated output and will be used to provide power to the Arduino and IMU. In order to measure the orientation of the robot an MPU-6050 Inertial Measurement Unit was used.

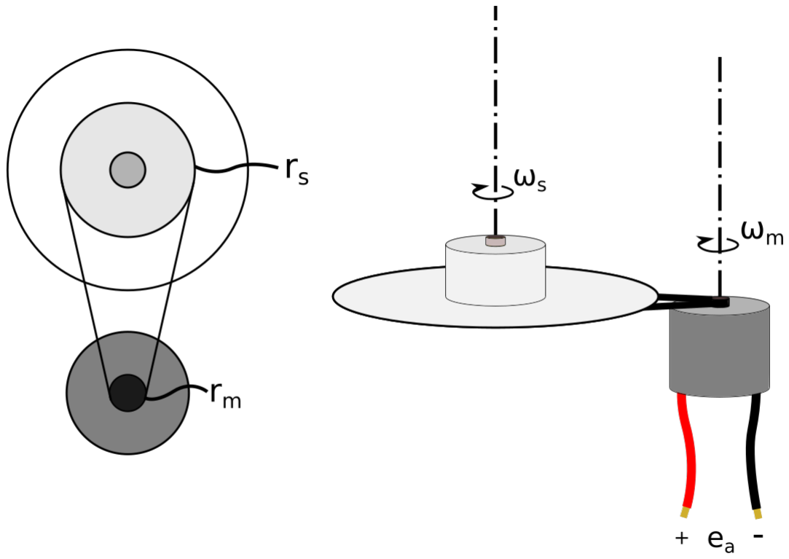
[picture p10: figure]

Figure 9: Overview of setup. ωs can be measured directly and related to ωm through geometry. The back emf, ea, can be measured directly as well.

### 4.2 Motor Parameter Evaluation

For a permanent magnet DC motor the following relationships hold[1]:

τ = KI

## 5 Software Design

### 5.1 Component Testing Software

### 5.2 Controller Software

## References

[1] Katsuhiko Ogata, System Dynamics, 4th edition, 2004.

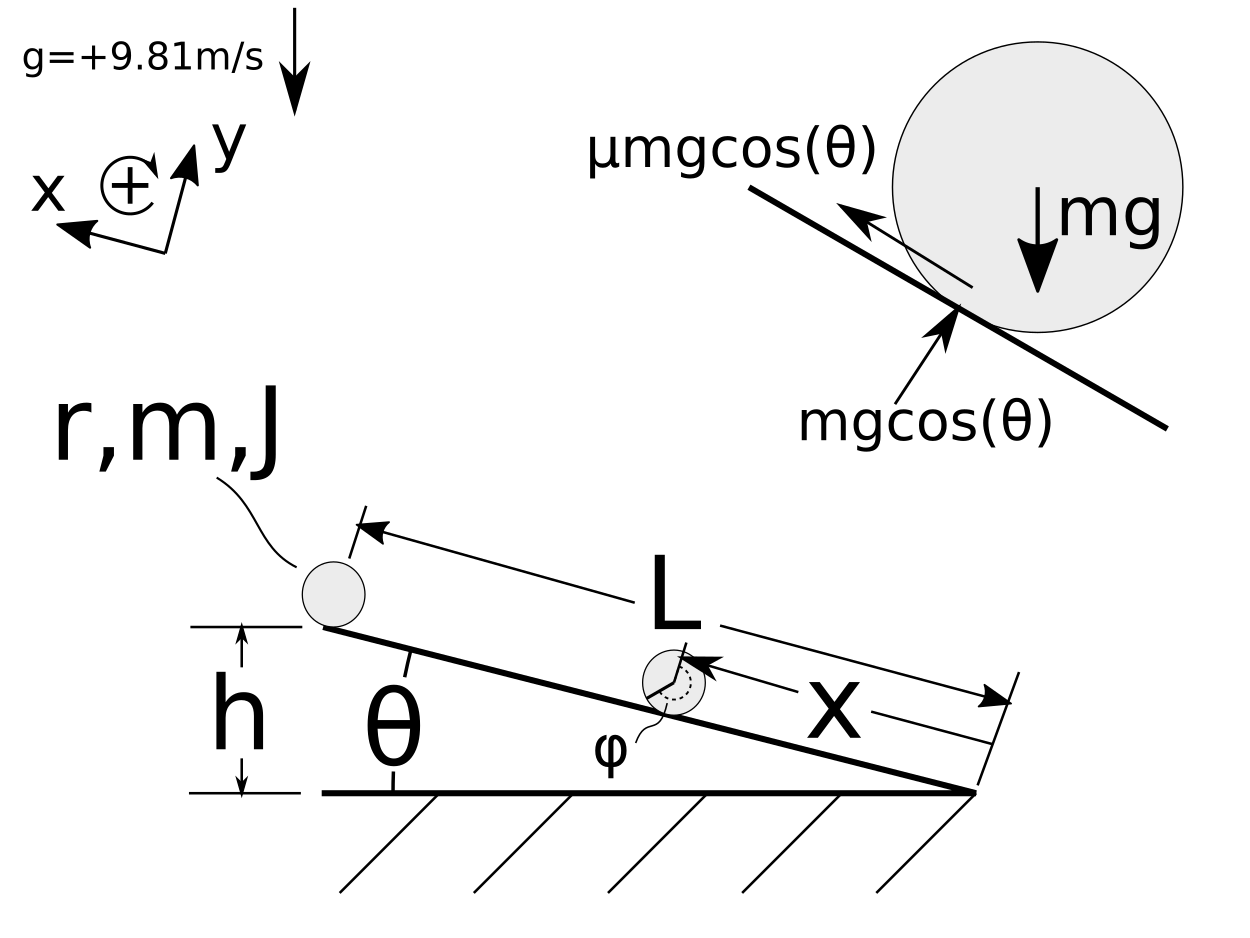
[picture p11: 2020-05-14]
Report/Images/Graphics/Body1_Mass_Properties.png

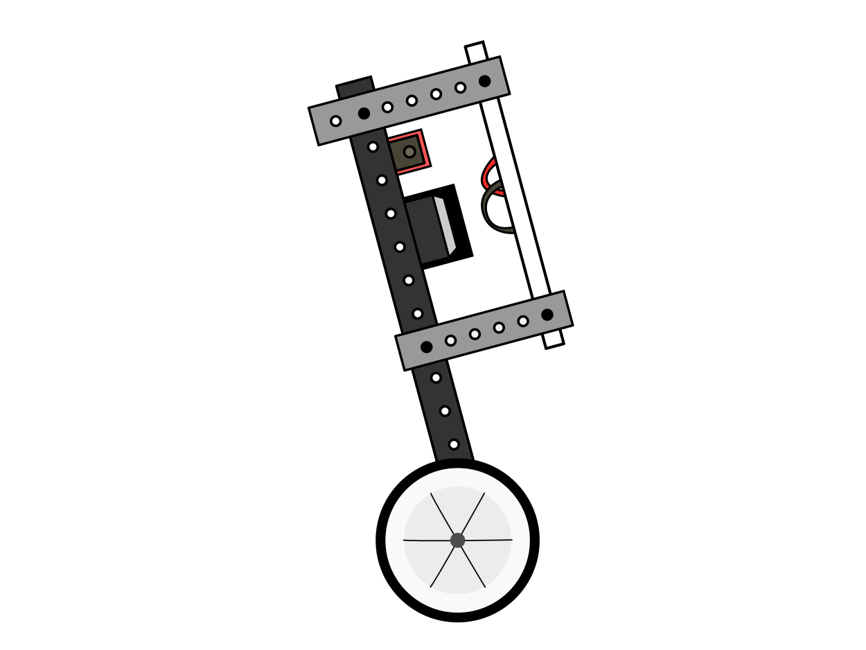
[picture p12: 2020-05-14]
Report/Images/Graphics/Robot_Body.png

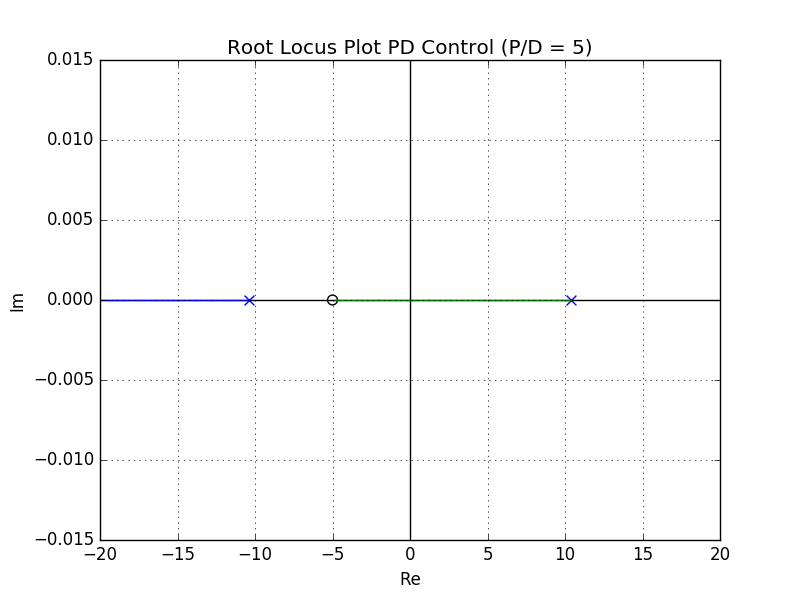
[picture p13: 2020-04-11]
Report/Images/SISO_Controllers/PDRL5.png

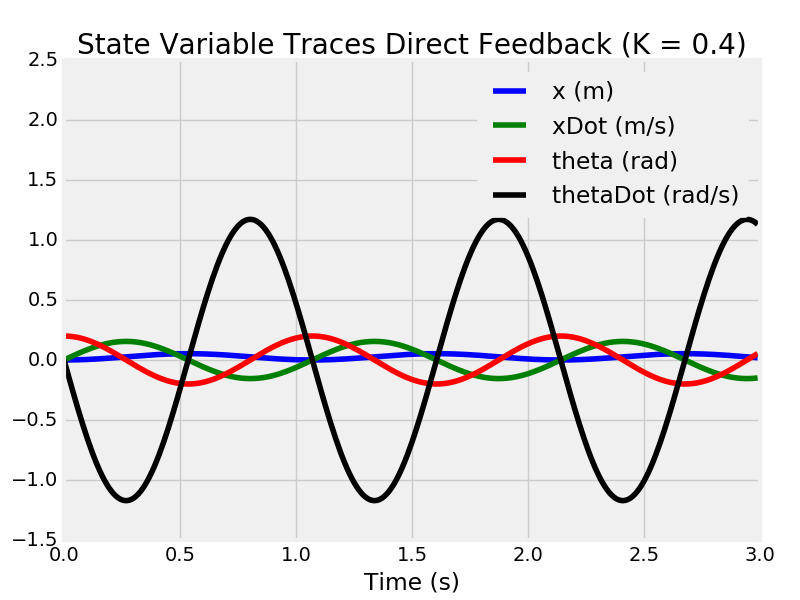
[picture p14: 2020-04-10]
Report/Images/SISO_Controllers/DFState Traces(k = 0,4).png

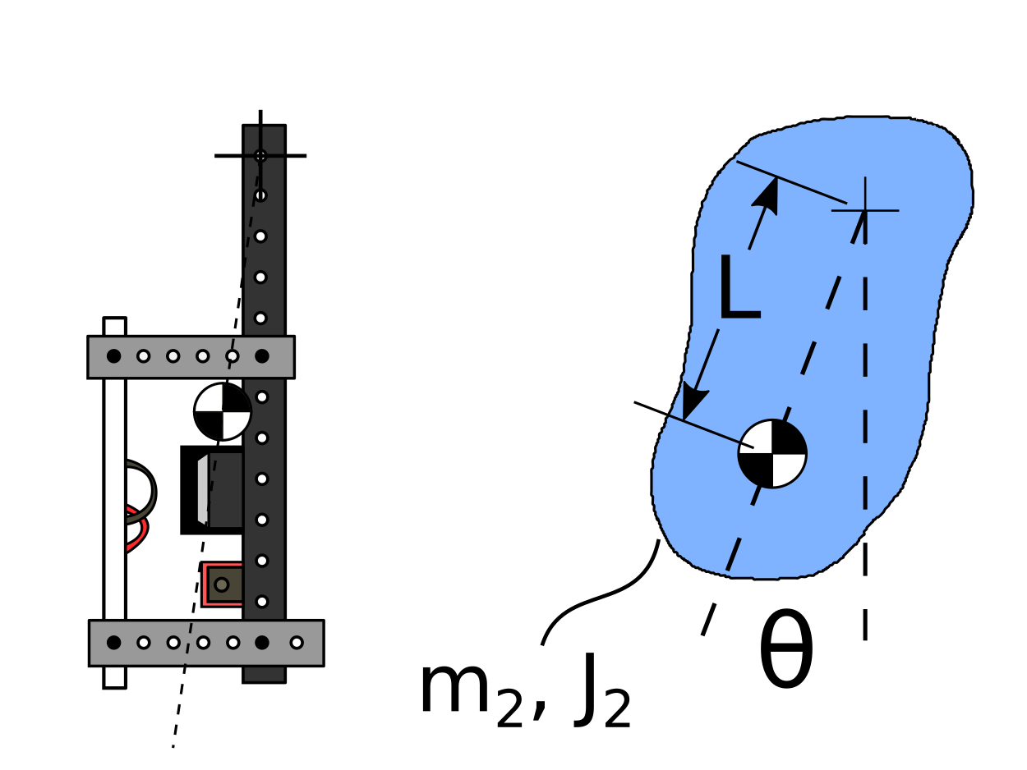
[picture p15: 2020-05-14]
Report/Images/Graphics/Body2_Mass_Properties.png

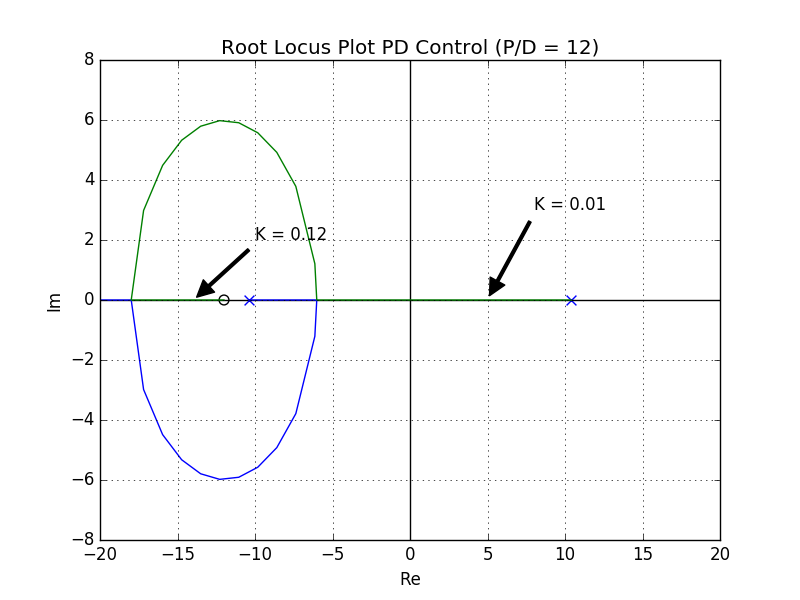
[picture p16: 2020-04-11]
Report/Images/SISO_Controllers/PDRL12.png

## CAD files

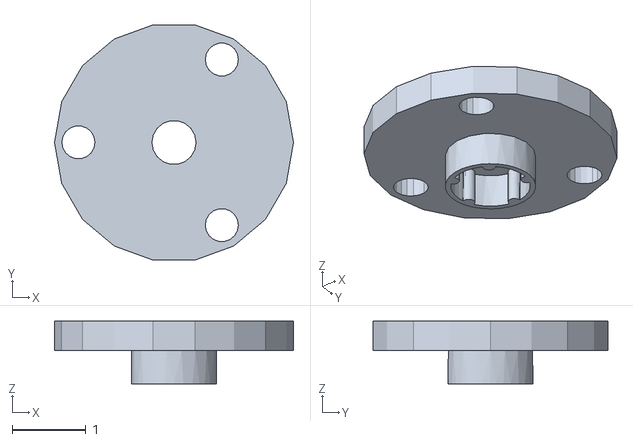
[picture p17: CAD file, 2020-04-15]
Part Models/Existing Parts/Right_Adaptor.stl
3.25 x 3.20 x 0.85

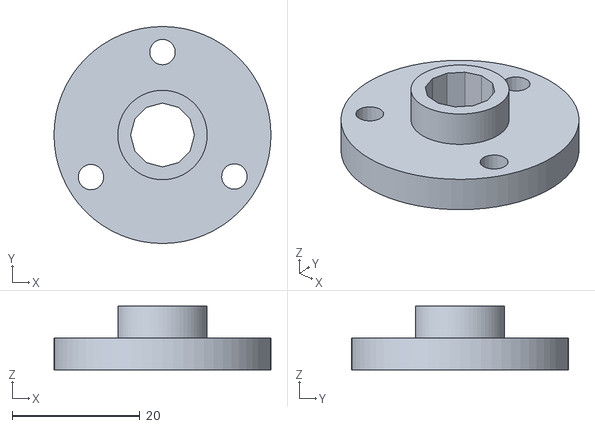
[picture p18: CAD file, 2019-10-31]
Part Models/Wheel Adaptor.stl
34.0 x 34.0 x 10.0

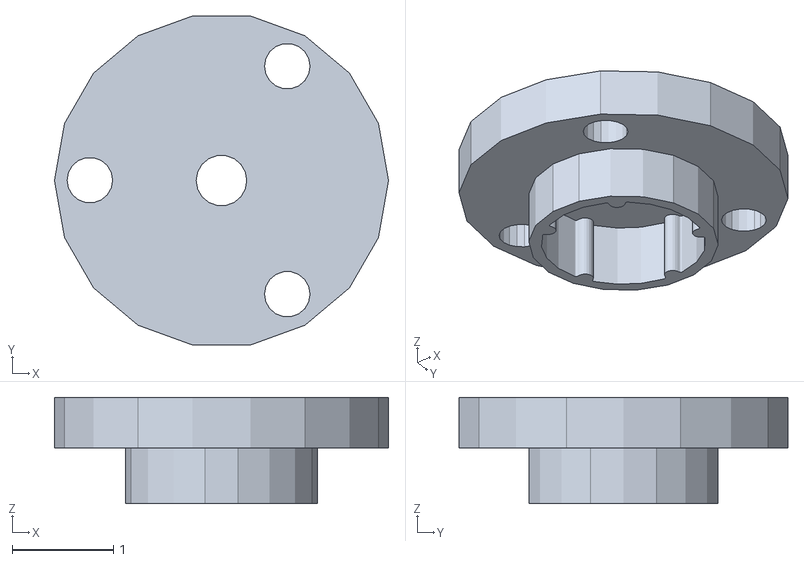
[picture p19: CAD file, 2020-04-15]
Part Models/Existing Parts/Left_Adaptor.stl
3.30 x 3.25 x 1.05

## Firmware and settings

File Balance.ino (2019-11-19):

#include <Wire.h>

//Interrupt and timer variables
const uint16_t T1_COMP = 500;   //=(16,000,000/prescale*freq) - 1. Sample time of 0.5s or 2Hz
const float controllerSampleTime = 1024*(T1_COMP + 1)/16000000.0;   //calculated based on T1_COMP

volatile boolean interrupted; //flag to check if interrupt has run

//MPU 6050 variables
uint8_t gyroSampleRate = 1;

const uint8_t SMPLRT_DIV = (uint8_t)((8/gyroSampleRate) - 1); //Calculate the sample rate division and fit it into an 8bit int
const uint8_t IMUADDRESS = byte(0x68); //I2C address of the MPU6050 (b1101000)

float ax, ay, az;
float gx, gy, gz;

const float gxBias = -2.75;   //Biases found for each gyro measurement. Found by averaging readings while on a flat surface
const float gyBias = 1.48;
const float gzBias = -0.54;

unsigned long time;   //timestamp of the last time the gyro was measured. used to calculate dt

//Application variables
boolean running;

float theta [3];              //angle of the robot
float thetaRef = -98.5;  //IMU is not mounted along flat axis so reference is not 0
volatile float u;         //controller input to actuators. Must be volatile since it's accessed from the interrupt service routine

float a = 0.98;   //Weighting variable for complimentary filter in state estimation algorithm

uint8_t count;  //counter to prevent pid loop from running before enough samples are taken

void setup() 
{
  Serial.begin(9600); //begin serial communication

  //MPU 6050 SETUP
  //Wake up the MPU 6050
  Wire.beginTransmission(IMUADDRESS);
  Wire.write(107);
  Wire.write(0);
  Wire.endTransmission(true);

  //Set the gyro full scale rate
  Wire.beginTransmission(IMUADDRESS);
  Wire.write(27); //register 27 sets the gyro rate
  Wire.write(0); //Set the gyro rate to +-250 deg/s
  Wire.endTransmission(true);
  
  //Set the accelerometer's full scale range
  Wire.beginTransmission(IMUADDRESS);  
  Wire.write(28); //Full scale value is stored in register 28
  Wire.write(0);  //0 corresponds to +- 2g
  Wire.endTransmission(true);

  //Set the gyroscope sample rate (Accelerometer sample rate is set at 1kHz)
  Wire.beginTransmission(IMUADDRESS); 
  Wire.write(25); //SMPLRT_DIV is stored in register 25. Sample rate is: gyroSampleRate = 8kHz/(1 + SMPLRT_DIV)
  Wire.write(SMPLRT_DIV);
  Wire.endTransmission(true);

  //L298N Setup
  //Pin 6 is the OC0A output so pin 12 is used instead
  pinMode(7, OUTPUT);   //2,7 backwards/forward motor 1
  pinMode(2, OUTPUT);
  pinMode(3, OUTPUT);   //3,4 backwards/forward motor 2
  pinMode(4, OUTPUT);
  pinMode(5, OUTPUT);   //5,6 pwm speed control motor 1 & 2
  pinMode(6, OUTPUT);

  cli();  //interrupts are allowed by default. stop them.
  
  //TIMER INTERRUPT SETUP
  TCCR1A = 0;
  TCCR1B = 0;   //make sure register is zeroed out before setting bits
  TCCR1C = 0;
  
  TCCR1B |= (1 << 3);    //Set to prescaler of 1024 and CTC mode. Other bits to select CTC are set by default in TCCR1A
  TCCR1B |= (1 << 2);
  TCCR1B |= (1 << 0);

  TCNT1H = 0;    //Reset timer0 and set the compare value
  TCNT1L = 0;
  
  OCR1AH = T1_COMP >> 8;  //set high byte
  OCR1AL = T1_COMP & 0xFF;  

  TIMSK1 |= (1 << 1);   //Compare TCNT1 to OCR1A

  //Application variables setup
  running = true;
  count = 0;
  
  Serial.println("Setup finished");

  sei();  //allow interrupts again
}

void loop() 
{
  if (running)
  {
    if (interrupted)  //do anything associated with the interrupt first to prevent too much time passing
    {
      interrupted = false;
      Serial.println("Interrupt");
    }

    count++;  //increment loop counter

    //update theta
    theta[2] = theta[1];
    theta[1] = theta[0];
    theta[0] = estimateState();
    Serial.print("Theta: ");
    Serial.print(theta[0]);
    Serial.print("    u: ");
    Serial.println(u);

    //control law is undefined if any theta terms are undefined so dont send motor commands if this is true
    if (count > 5)
    {
      //interpret the controller command from the ISR
      interpretMotorCommand (u);
    }
  }
}

/**State estimation function will consist of a complimentary filter to
 * combine the accelerometer and gyroscope measurements into a single
 * value that will be relied on by the system.
 */

float estimateState ()
{
  readIMU ();   //update the values in the global readings
  
  /**Estimate the time delay from when the state was last estimated. State estimation
   * runs as fast as possible and is assumed to be a continuous process.
   */
  unsigned long dt = micros() - time;
  time += dt;             //increment time by dt
  
  float gtheta, atheta; //estimates of theta derived from either gyroscope or accelerometer measurements

  gtheta = theta[0] + gx * dt/1000000;   //need to define dt. Divide by 1000000 to convert to seconds
  atheta = atan2(ay,az)*180/PI; //Use atan2 function and convert to degrees.

  // A complimentary filter is defined as z = ax + (1-a)y. Calculate and return this value
  return a*gtheta + (1-a)*atheta;
}

  /**Interpret the control input u as a motor command. This will
  * be done linearly though the scaling may have to be adjusted depending on
  * the control law implemented do to the limits imposed on pwm variables 
  * (0 - 255).
  */
void interpretMotorCommand (float u)
{
  if (u > 0)
  {
    digitalWrite (7, LOW); //Forward
    digitalWrite (2, HIGH);
    digitalWrite (3, LOW);
    digitalWrite (4, HIGH);
  }
  else
  {
    digitalWrite (7, HIGH);  //Reverse
    digitalWrite (2, LOW);
    digitalWrite (3, HIGH);
    digitalWrite (4, LOW);
  }

  analogWrite (5, abs(u)); //set the pwm speed proportional to u. Sign is taken care of above
  analogWrite (6, abs(u));
  
  return;
}

/**Read the sensor into global variables for each relevant measure. Global variables
 * for gyro readings are gx,gy,gz and for accel are ax,ay,az.
 */
void readIMU ()
{  
  //The IMU automatically updates each sensor's reading at the rate set in the registers.
  Wire.beginTransmission(IMUADDRESS);
  Wire.write(59); //Read addresses 59-72 are sensor data
  Wire.endTransmission(false);  //For burst read don't send a stop signal

  Wire.requestFrom(IMUADDRESS,14); //Request 14 bytes of data from IMU (Register already set to start at 59)

  if (6 <= Wire.available())  //if all of the data is available
  {   
    ax = (Wire.read() << 8 | Wire.read()) / 16384.0;  //Read Accelerometer
    ay = (Wire.read() << 8 | Wire.read()) / 16384.0;
    az = (Wire.read() << 8 | Wire.read()) / 16384.0;

    Wire.read();  //Ignore the temperature sensor in the middle
    Wire.read();

    gx = ((Wire.read() << 8 | Wire.read()) / 131.0) - gxBias;  //read gyro
    gy = ((Wire.read() << 8 | Wire.read()) / 131.0) - gyBias;
    gz = ((Wire.read() << 8 | Wire.read()) / 131.0) - gzBias;
  }

  Wire.endTransmission(true); //send stop signal to terminate transmission

  return;
}

/**Interrupt service routine will be used to calculate motor command u. The actual writing
 * of u to the motors will be done in the main loop function outside of interrupts.
 */
ISR (TIMER1_COMPA_vect)
{
  static float kp = 300;
  static float ki = 0;
  static float kd = 50;

  float a = (kp + ki*controllerSampleTime/2 + kd/controllerSampleTime);
  float b = (-kp + ki*controllerSampleTime/2 - 2*kd/controllerSampleTime);
  float c = kd/controllerSampleTime;

  u = float(a*(thetaRef - theta[0]) + b*(thetaRef - theta[1]) + c*(thetaRef - theta[2]));  //apply proportional feedback
  
  interrupted = true;
}

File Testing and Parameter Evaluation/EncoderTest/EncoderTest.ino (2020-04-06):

class PID
{
  private:
  float kp;  //Controller gains
  float ki;
  float kd;

  int32_t err [2];     //Tracked variables
  int32_t accErr;
  float diff;       //float because it is read from encoder
  
  int32_t lastCount;  //previous position for speed calculations
  int32_t reference;  //reference position specified in counts

  int32_t lastU;

  float t; //time step for the controller (seconds)

  public:
  PID (float p, float i, float d, float dt)
  {
    kp = p;
    ki = i;
    kd = d;

    err [0] = reference;  //initial errors are the entire distance from reference to 0
    err [1] = reference;

    reference = 0;

    t = dt;
  }

  /**main function to generate input signal. Assumes the time step dt is respected by the main
   * program. A timer interrupt is to be used to ensure it is. The controller assumes continuous
   * time so dt must be small to prevent errors.
    */
  int32_t generateInput (int32_t count)
  {
    float a = (float)(kp + ki*t/2.0 + kd/t);
    float b = (float)(-kp + ki*t/2.0 - 2*kd/t);
    float c = (float)kd/t;

    lastU = (int32_t)(lastU + a*(reference - count) + b*err[1] + c*err[2]);   //Discrete time pid loop

    err[1] = err[0];
    err[0] = reference - count;

    return lastU;
  }

  void getSpeed ()
  {
    return diff;
  }

  void printAccErr ()
  {
    Serial.print ("accErr: ");
    Serial.println(accErr);
  }

  void printErr ()
  {
    Serial.print ("Err: ");
    Serial.println (err[0]);
  }

  void printLastU ()
  {
    Serial.print ("U: ");
    Serial.println (lastU);
  }

  void printReference ()
  {
    Serial.print ("Reference: ");
    Serial.println(reference);
  }

  void setReference (int32_t ref)
  {
    reference = ref;
  }
};

/** Code to run the AEDS-96xx optical encoder. Due to the speed of the arduino only a quarter of possible states
 *  are used. This class assumes that the main program has already set up the appropriate pins as inputs. The 
 *  constructor of this class however attaches the appropriate interrupts.
 *    It is possible that in the future the micros function may be replaced with direct register reads on an 
 *  internal timer to increase accuracy and speed up the functions.
 */
class QuadEncoder
{
  private:
  const uint16_t COUNTS = 700; //Encoder wheel believed to be 700 count/rev
  
  volatile int32_t positionCounts [2];   //last and current positions. Measured in counts
  volatile float velocity;        //velocity measure in counts per second

  uint8_t channelAPin;  //Channel A triggers interrupt
  uint8_t channelBPin;  //Channel B checks direction

  public:
  QuadEncoder (uint8_t pin1, uint8_t pin2)  //Constructor method
  {
    positionCounts[0] = 0; //Relative encoder always starts at position 0
    positionCounts[1] = 0;
    velocity = 0; //Velocity is completely dependent on position in this application

    channelAPin = pin1;   //channelAPin has interrupt attached and triggers updates
    channelBPin = pin2;   //channelBPin is checked in the interrupt to determine direction 
  }

  void displayState ()
  {
    if (Serial) //will only work if serial communication is running
    {
      Serial.print ("Position: ");
      Serial.println (positionCounts[0]);
      Serial.print ("Velocity: ");
      Serial.println (velocity);
    }
  }

  int32_t getPosition ()
  {
    return positionCounts[0];
  }

  float getVelocity ()
  {
    return velocity;
  }

  //Read encoder and update position and velocity
  void readEncoder ()
  {    
    if (digitalRead(channelBPin))
    {
      positionCounts[0]++;
    }
    else
    {
      positionCounts[0]--;
    }
  }

  void updateVelocity ()
  {    
    //dt is constant (0.1s)
    velocity = (float)((positionCounts[0] - positionCounts[1])/(0.1)); //dt is constant since the motor is moving slow

    positionCounts [1] = positionCounts[0]; //update the value of the previous position
  }
};

                            //GLOBAL VARIABLE DEFINITION
boolean running = true;
volatile boolean changed = false;

unsigned long lastControllerTime;

PID pid (1.5,1,0,0.01);  //define pid object
QuadEncoder enc1 (2,3);   //initialize encoder 1 object

void setup() {  
  lastControllerTime = 0;
  
  pinMode(2, INPUT);  //Pin 2 is the interrupt pin
  pinMode(3, INPUT);
  pinMode(5, OUTPUT); //pwm output for forward motor command
  pinMode(6, OUTPUT); //pwm output for reverse motor command  
  pinMode(13, OUTPUT);
  
  digitalWrite(13, HIGH); //Turn on the encoder. Will remain on for entirety of sketch

  //Setup timer interrupt to update velocity
  noInterrupts ();  //turn off interrupts

  TCCR1A = 0;   //Set all bits to 0 to be changed later
  TCCR1B = 0;

  TCCR1B |= (1 << WGM12); //CTC Mode on timer 1 comparing to OCR1A
  TCCR1B |= (1 << CS12);  //256 prescaler

  TIMSK1 |= (1 << OCIE1A);  //Enable compare match interrupt for timer 1
  
  OCR1A = 6249; //10 Hz
  TCNT1 = 0;   //initialize counter to 0

  interrupts ();  //make sure interrupts are turned back on

  //Trigger interrupt to read encoder on rising edge of channel A. Checking only A halves resolution
  attachInterrupt(INT0, enc1Read, RISING);   //Hacky solution to avoid problem of calling instance method from interrupt.

  Serial.begin(9600); //Start serial communication
  Serial.println("Initialized");

  pid.setReference (200); //Change the reference value
}

void loop() {
  if (running)
  {
    if (millis() - lastControllerTime > 10)
    {
      commandMotors(pid.generateInput(enc1.getPosition())); //update motor command
      lastControllerTime = millis();
    }

    Serial.println(enc1.getPosition());
  }

  if (Serial.available() > 0)
  {
    handleSerialInput ();
  }
}

/**Function to process the input u generated by the controller and convert it into motor
 * voltages. The motor output is insignificant at values less than ~125 due to the friction
 * in the encoder so care must be taken when tuning a linear controller.
 */
void commandMotors (int32_t u)
{
  //Serial.println (u);
    
  if (u > 255) //constrain u to the limits of analogWrite function
  {
    u = 255;
  }
  if (u < -255)
  {
    u = -255;
  }

  if (u >= 0)
  {
    analogWrite (5, u);
    analogWrite (6, 0);    //Motor will lock up if the other pin isn't written to 0
  }
  else
  {
    analogWrite (5, 0);
    analogWrite (6, abs(u));
  }
}

void handleSerialInput ()
{
  char received = Serial.read();

  switch (received)
  {
    case 'q':
      analogWrite (5,0);
      analogWrite (6,0);
      running = false;
      break;
    case 'e':
      pid.printErr ();
      break;
    case 'i':
      pid.printAccErr ();
      break;
    case 'r':
      pid.printReference ();
      break;
    case 'u':
      pid.printLastU ();
      break;
    case 'a':
      commandMotors (-2550);
      break;
    case 's':
      commandMotors (2550);
      break;
    case 'x':
      enc1.displayState ();
      break;
  }
}

void enc1Read ()
{
  enc1.readEncoder ();
  changed = true;
}
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

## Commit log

2019-10-28 Added references folder with MPU6050 docs and Balance.ino which will hold all arduino code.
2019-10-29 Added models folder and wheel adaptor model
    [Wheel Adaptor.stl]
2019-10-31 Modified Wheel Adaptor.stl to fix measurement of holes
    [Wheel Adaptor.stl]
2019-11-01 Balance.ino: Added calculateMotorSpeed() and moved sensor reading code to readIMU()
2019-11-01 Balance.ino: Added estimateState() using a complimentary filter to combine accelerometer and gyro measurements
2019-11-01 Updated read me and verified the filter was outputting reasonable readings.
2019-11-01 Balance.ino: added evaluateControlLaw() and started with a 'continuous time' PID controller in a round robin configuration. Will test once wheel adapter is printed and robot is functional.
2019-11-01 Updated readme to reflect use of 'continuous time' PID controller to test base functionality
2019-11-05 Balance.ino: Added initial delay to allow battery to be installed without winding up integrator and timeout to stop program without removing batteries.
2019-11-07 Balance.ino: Fixed weak motor issue by switching pin 6 for pin 12 in calculateMotorSpeed()
    [Balance.ino]
2019-11-10 Balance.ino: Restructured entire file to deal with timer interrupt issues. Simplified the organization of the functions to hopefully make more readable and attempted to implement some embedded best p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
    [ISR_Test.ino]
2019-11-19 Added reference material on bode integrals
2019-12-02 Modified readme to reflect failed tests of simple pid control. Redesign of mechanical portion of system required including new motor adn transmission is required to reduce nonlinearities.
2019-12-12 Completed nonlinear dynamic model of mechanical system using scipy
    [Wheel Adaptor.stl]
2020-03-15 Restructured pid loop into a pid object to simplify access to variables and clean up main loop.
2020-03-15 Forgot to move encoder test folder into project directory prior to last commit
2020-03-16 Began repackaging encoder coder into class QuadEncoder to simplify access. Need to figure out how to access object method from interrupt or a better way to structure this.
2020-03-16 Finished moving encoder functions into class. Tested and working.
2020-03-18 Finished coding velocity estimator using constant dt. Calculated motor constant with velocity estimate and external measurements. Minor formatting changes to make code more clean mostly in input hand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
2020-03-19 Fixed sign error on derivative term of pid controller. Can command motor to appropriate position in reasonable time with and without overshoot.
    [EncoderTest.ino]
2020-04-15 Reorganized Motor_Evaluation sketch to break each class into its own file. Greatly simplified code to increase readability.
    [Left_Adaptor.stl, Right_Adaptor.stl]
2020-04-20 Added several sections to report. Reorganized classes for driver, encoder, and pid loop in motor testing file.
    [Torque_Constant_Data.csv]
2020-04-20 Replaced velocity estimator to better estimate constant speeds to allow speed control. This will help estimate current dependence on pwm input for different speeds.
    [Motor_Evaluation.ino, QuadEncoder.cpp]
2020-04-24 Rewrote QuadEncoder class to setup interrupts within constructor and greatly speed up execution. Interrupt Service Vector was changed to pin change interrupt to provide generality. Currently programm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
